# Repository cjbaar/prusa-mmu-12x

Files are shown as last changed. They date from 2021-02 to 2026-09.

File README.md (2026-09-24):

# ⚠️ **WARNING** ⚠️

Prusa is now blocking tool commands for community mods like this
on the CoreOne/L latest firmware. Unless they decide to reverse course,
upgrading past firmware version 6.5.7 will break this version of the
MMU3 with a hard-reset and error message mid-print. The firmware has
been locked-down to accept only T0-T4 commands. Working around this
now requires comiling custom firmware, and invalidating your printer's
warranty to apply it.

To say I am disappointed with this approach is an understatement. This
is not in the spirit of open source on which Prusa was founded.
I will not be purchasing any more printers from Prusa Research in the future.

# Prusa MMU2/MMU3 Modification for 12 Filaments
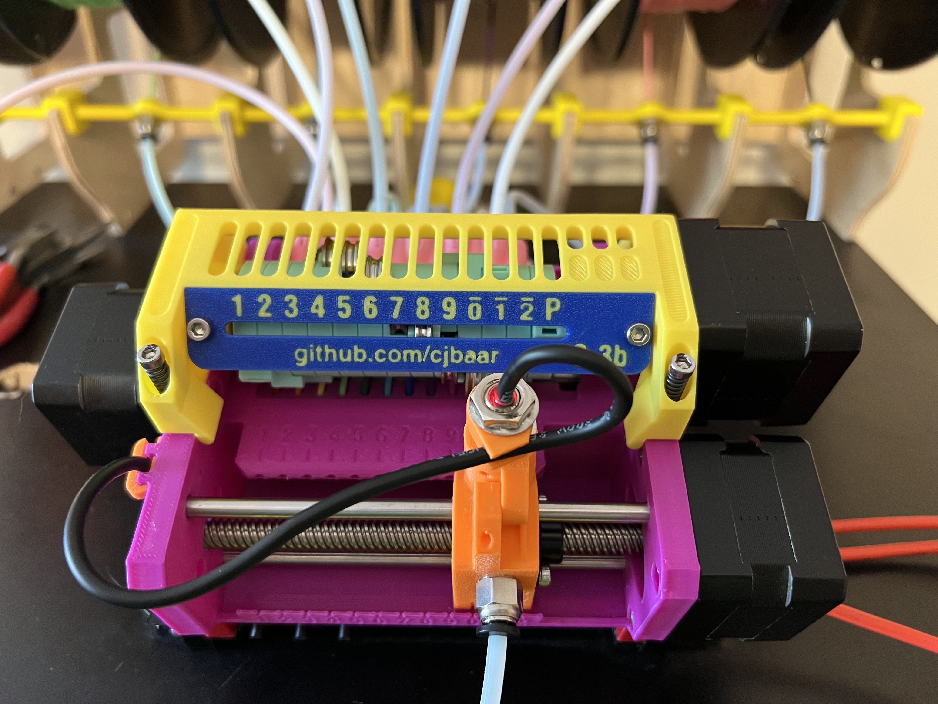
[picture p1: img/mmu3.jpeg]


## Overview

This is the result of several months of designing and testing new ideas for increasing the filament count of the Prusa MMU2S. (And then more testing and re-designs for the MMU3.)
I tried several variations, but ended up coming back to something that is largely based
on the original Prusa model. Some of the major adjustments include:
* increased filament count from 5 to 12
* reversed position of pulley and idler motors, to maximize the use of the 110mm pulley shaft
* moved FINDA to the rear of the selector, in an attempt to minimize issues where the filament clears the ball but then still fails to fully retract
* quick-release insert for FINDA sensor, for ability to clean or check ball chamber without re-calibration of FINDA height
* selector has integrated threads for PTFE quick-connect
* moved control board beneath the body (inspiration thanks to [univeraljoint](https://www.thingiverse.com/universaljoint/about))
* additional bracket mounting options
* selector does not include the cutter

As of October 2024, this project has been updated to include the MMU3 with the Mk4.
New features now also include:
* a new idler alignment gauge of the front side of the upper frame
* a streamlined idler design
* a smaller inlet that uses the PTFE collets instead of M10 screw connectors
* a cover panel for the power connection board

## The Disclaimer

*These items and related code are provided as-is, with no warranty -- express or implied -- and I cannot personally guarantee that it will function and/or not break your printer. Nothing here, of course, is officially endorsed or supported by Prusa.*

*(That being said, I -- and others -- have had a great deal of luck using this model, or I wouldn't be sharing it.)*

## Firmware

See update notes on version [3.0.4](https://github.com/cjbaar/prusa-mmu-12x/discussions/51).

### The Good News

Prusa has completely re-written the firmware for the MMU3. It is incredibly
clean and organized, and makes wonderful and proper use of configuration variables.
*(Thank you Prusa!)*
We no longer need to use custom firmware anymore, for either the MMU board
or the printer itself!

You can use the [`config.h`](./firmware/config-mmu3-mk4-12x.h) file provided here, and do your
own build with the [Prusa MMU Firmware](https://github.com/prusa3d/Prusa-Firmware-MMU) repo. I would generally encourage you to become familiar with the build process if you want to proceed
with this project. I will probably not be compiling this into every new version that Prusa
releases. However, you can download a compiled version of the current (as of now)
[3.0.3 firmware here](./firmware/cjb_fw_mmu3_3.0.3-x12.hex), or view
[my firmware fork here](https://github.com/cjbaar/Prusa-Firmware-MMU-12x).

NOTE: This version of the MMU3-12x will function exactly like the
stock Prusa MMU3, as it is entirely their firmware with a few different distance
numbers. It will use the new communication protocols, and report error messages
back to the printer screen. I personally found my interface "tweaks" easier to use and
understand, but this keeps things simpler. With the amount of work Prusa has to the
stock code, it just doesn't make sense to try re-writing it anymore.

### The Potential (Unknown) News

At the moment, flashing the MMU firmware is a relatively simple process, and the current
stock printer firmware does not block filaments above slot 5 -- even though it does not
understand how to process or access them from the menu functions.

As of now (Oct 2024), Prusa is currently working toward a firmware model wherein
the printer will retain a 
copy of the MMU firmware, and be responsible for updating it as necessary. I have no
idea how those changes will affect the ability to side-load custom firmware onto
the MMU directly. If we have to get into changing the printer firmware itself, things
become more complicated. We will have to wait and see for now.

__Update 03/2026__: I am still using stock printer firmware (6.5.3) without issue. There is no need to use custom printer firmware with the MMU3.

## Hardware

### Printed Parts
Print one of each included STL file, with the following exceptions:
* choose either m6 or m10 thread for selector base
	* or original m5 heat-set remix, thanks to [obe](./remixes/obe)
* choose bracket type (traditional frame mount or table-top)
* print four copies of idler-rings.stl

I printed all parts with on a Prusa Mk4 using the "Structural" input-shaping profile.
All are printed with 0.2mm layers and 20% infill.

I also print everything with PLA, because I get better consistency and tolerances for bearings and general fit. In my experience, printing the same model in PETG (or other material) may make some pieces harder to fit together.

For the "lower" model, there is a related mod file, which I recommended printing with 100% infill. The selector cap might also need to be 100% infill.

### Additional Parts

The following pieces are required for assembly. Items in italics may not be included in the original Prusa MMU3, but should be easily found on Amazon (or your world-domination retailer of choice).

#### Lower
* (1x) Prusa MMU "Pulley" motor (110mm d-shaft)
* (1x) Prusa MMU "Selector" motor (120mmx8mm lead screw)
* (12x) m3x10mm screw
* (6x) m3 square nut
* (4x) 625Z bearing
* (2x) 5mmx120mm steel rod
* *(7x) 12mmx12mmx5mm drive gear (40T)*\
	NOTE: I have a hard time finding actual 12mm wide gears now. All the ones I have purchased lately on Amazon claim to be 12mm, but are actually only 11mm. These may cause issues with filament allignment.

#### Upper
* (1x) Prusa MMU "Idler" motor (std d-shaft)
* (3x) m3x10mm screw
* *(2x) m5x16mm screw*
* (2x) m3x30mm screw
* (2X) m3x6mm screw
* (2x) m3x15mm spring
* (2x) m3 square nut

#### Idler
* *(12x) m3x20mm screw*
* (12x) m3 hex nut
* *(1x) 608RS bearing*
* *(12x) 4x13x4mm u-shaped bearing*
* *(1x) 5mmx100mm steel rod*

#### Microcontoller Unit (MCU)
* *(4x) m3x14mm screw*
* *(3X) m3x12mm screw*
* (1X) m3x6mm screw
* (3x) m3 hex nut
* (1x) m3 square nut

#### Inlet
* *(2x-6x) m2x16mm screw*
* *(2x-6x) m2 hex nut*
* (12x) PTFE collet

#### Selector
* *(2x) m3x8mm screw*
* *(2x) m3x16mm screw*
* (2x) m3 square nut
* (2x) m3 hex nut
* (1x) T8 plastic lead screw nut
* *(1x) m10 OR m6 PTFE quick-fit connector*
* (2x) 5mm brass sleeve, cut to 20mm length
* (1x) FINDA sensor
* (1x) Sensor ball

#### Brackets
* *(2x) m3x8mm screw*

## Images
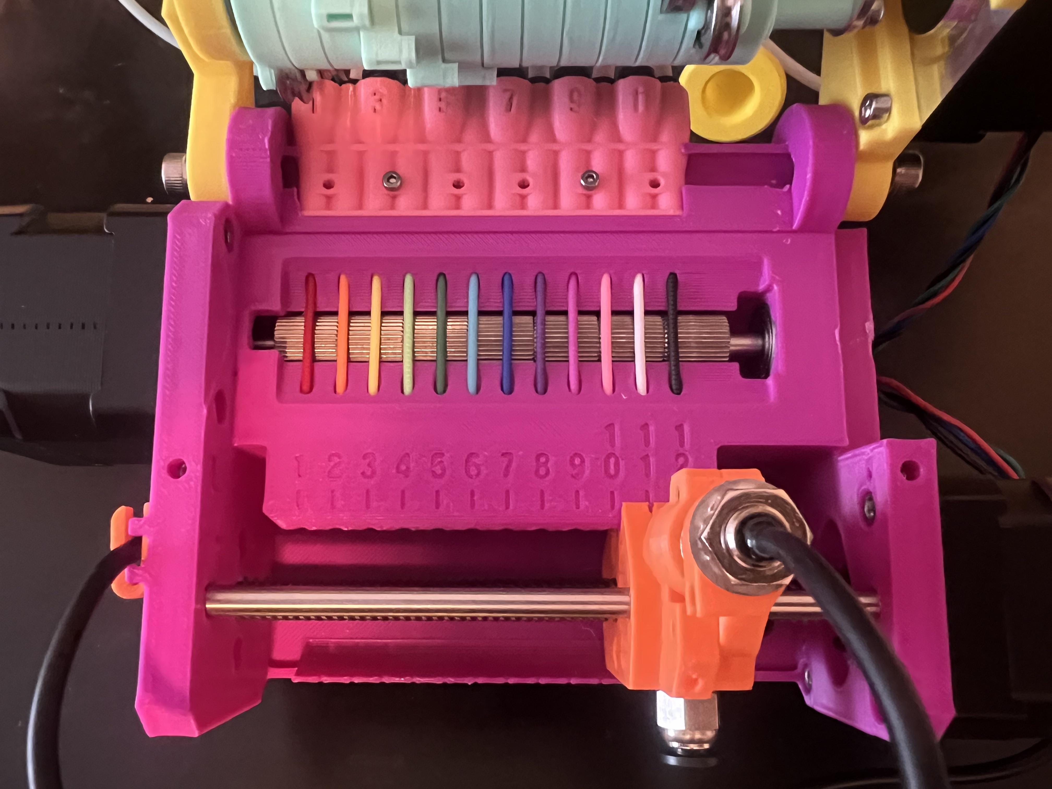
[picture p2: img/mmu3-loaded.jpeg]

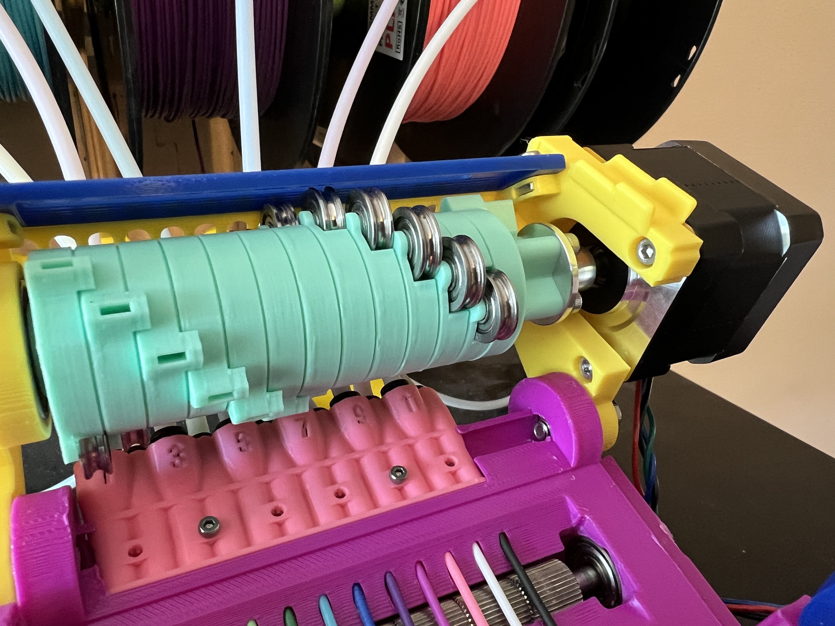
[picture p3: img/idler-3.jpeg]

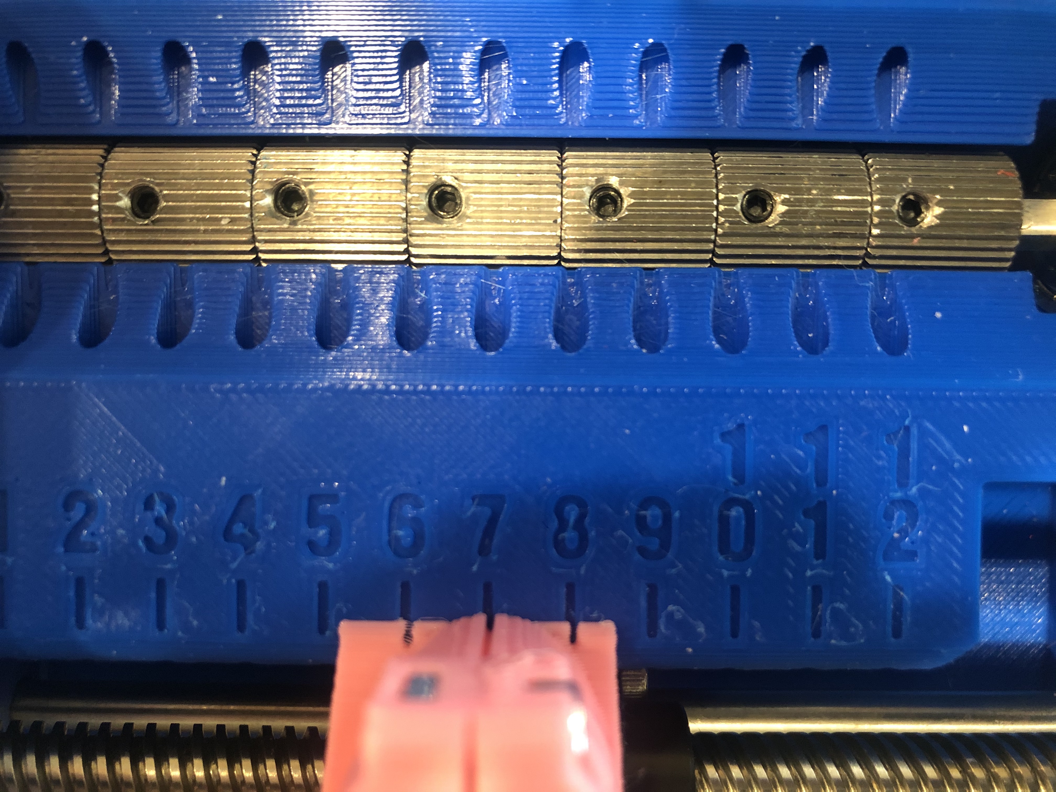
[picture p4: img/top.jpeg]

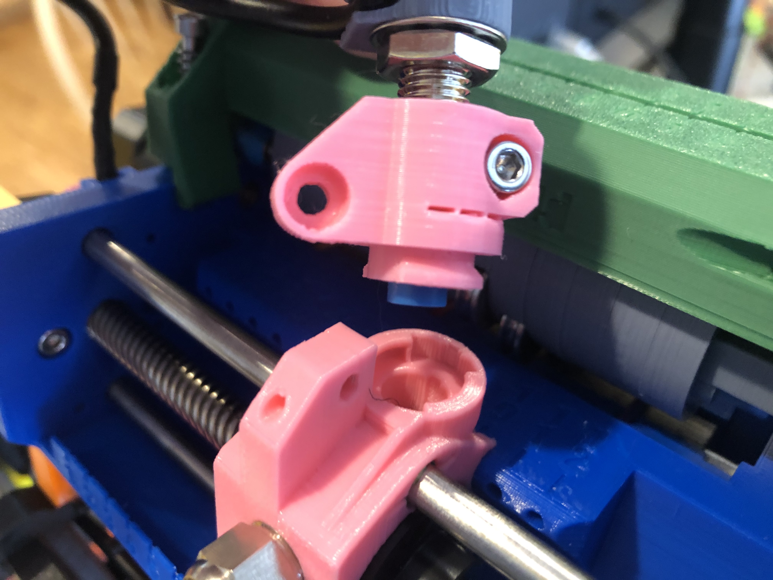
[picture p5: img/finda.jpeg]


## Testing
Full setup with spool rewinders from [VincentGroenhuis](https://www.thingiverse.com/thing:3781815/files)

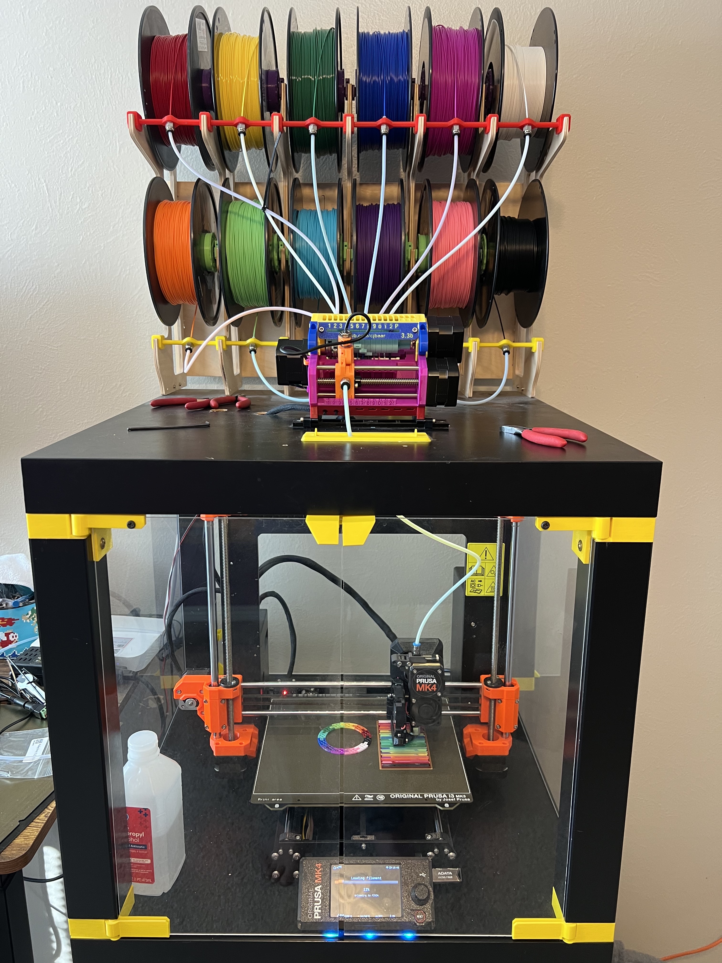
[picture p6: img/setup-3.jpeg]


## Output
A successful 12-color print.

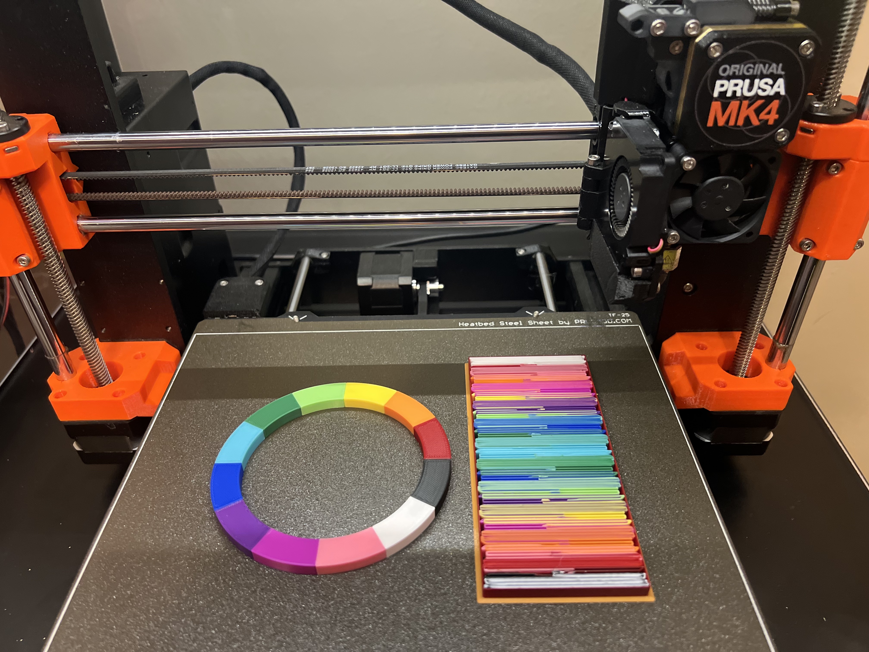
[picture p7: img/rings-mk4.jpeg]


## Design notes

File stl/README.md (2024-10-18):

# Prusa MMU Modification for 12 Filaments

## Directory

#### v1.4
Files for the older (MMU2/MMU2S+Mk3) version.

#### v3.3
Current files for the MMU3+Mk4.

*To avoid confusion (or perhaps incur more of it), I skipped to version 3,
to align with the MMU version number.*

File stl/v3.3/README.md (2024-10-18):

# Assembly Tips

As this project has started to gain popularity, several people have asked for more detailed
build instructions. Being a pet project, I don't have any official documentation. In general,
the files provided assume that you have previously built the stock Prusa MMU3, and are probably
re-using many of the parts. Below are some of the major differences from the stock model.

## Pulley

The pulley motor is moved to the left, to make full use of its length. Install a 625Z bearing
on each side of the pulley chamber, and start feeding the motor shaft in from the left of the
unit. As you go, install the seven 40T gears. As shown here, try to align the gears so that no
filament will end up on a grub screw. The even-numbered filaments will end up in the very narrow
space between the edge of a gear and its grub screw.

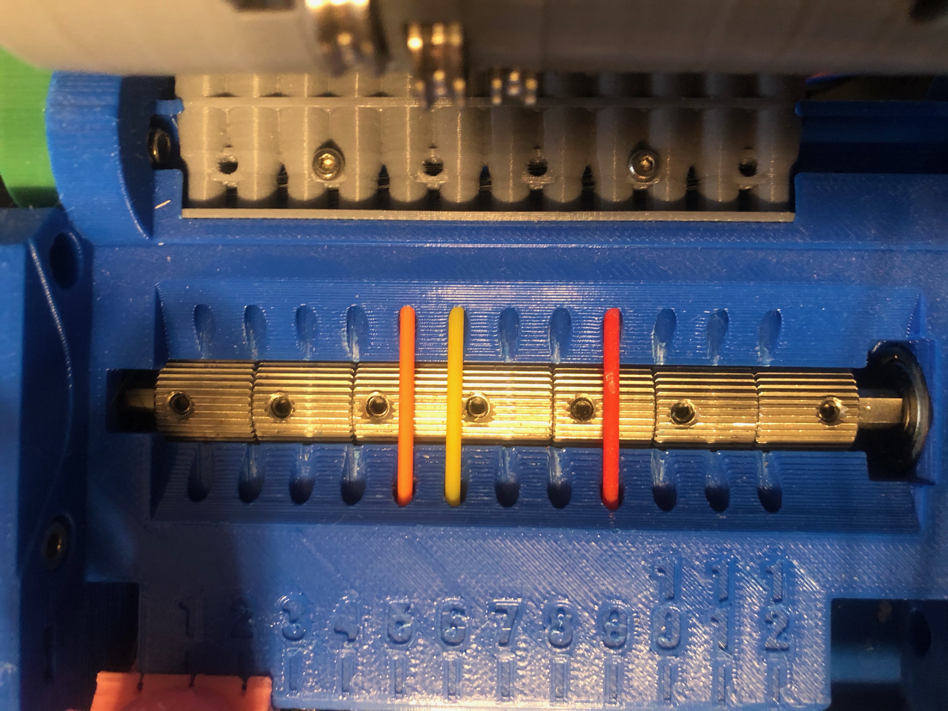
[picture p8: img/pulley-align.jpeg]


## Inlet

The inlet now uses the PTFE collets including with the MMU3 kit. It needs 12, so I used
the ones from the buffer/roller kits as well (I don't use them). If you don't have enough,
or you prefer the M10 screw PTFE locks, you can print the old inlet from the v1.4 folder.
Both models fit in the lower frame the same, and can be held with a couple of M2 screws.

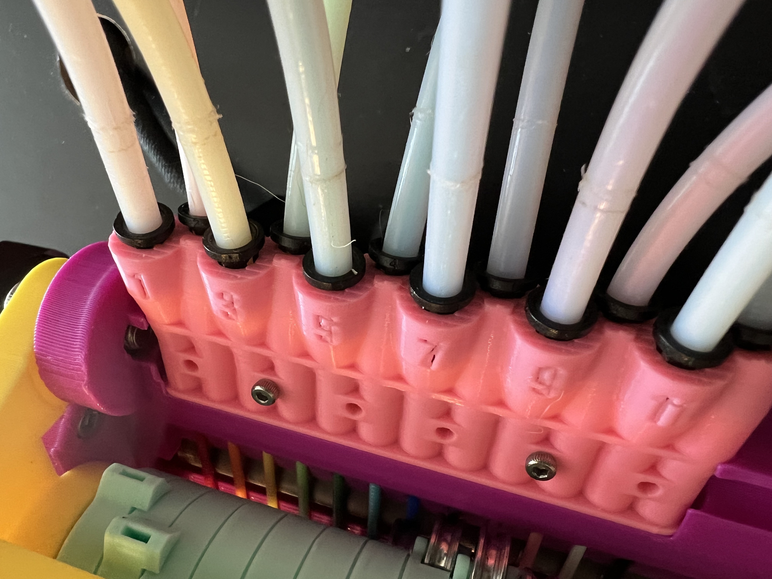
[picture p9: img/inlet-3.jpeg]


## Idler

This is the most major change, as the idler has to be assembled from many pieces. Start with
the a ring labeled "3" for the bottom, and add the rings in groups of three. Each ring
has a printed number (1,2,3) on the bottom, so install in order, and make sure the screw holes
line up. Place hex nuts in the end piece, and in each "#3" piece, and then after each set
install the M3 screw. These screws are probably optional, but I use them to help keep the
alignment snug. Do not tighten the screws past the point where they are seated, or it could
compress the overall size of the idler.

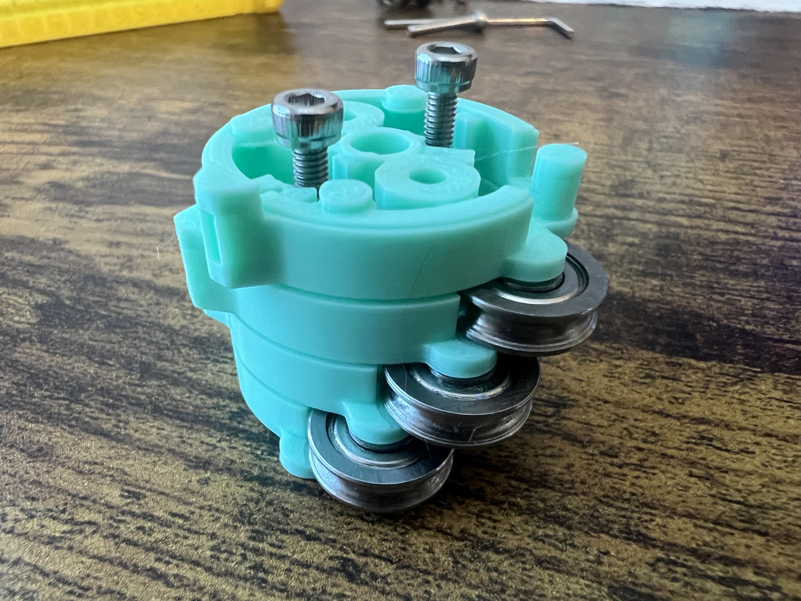
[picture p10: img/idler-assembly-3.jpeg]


Before installing the top end, make sure to inset 4x M3 hex nuts. These will hold the metal
motor mount (included with the Prusa MMU3 kit).

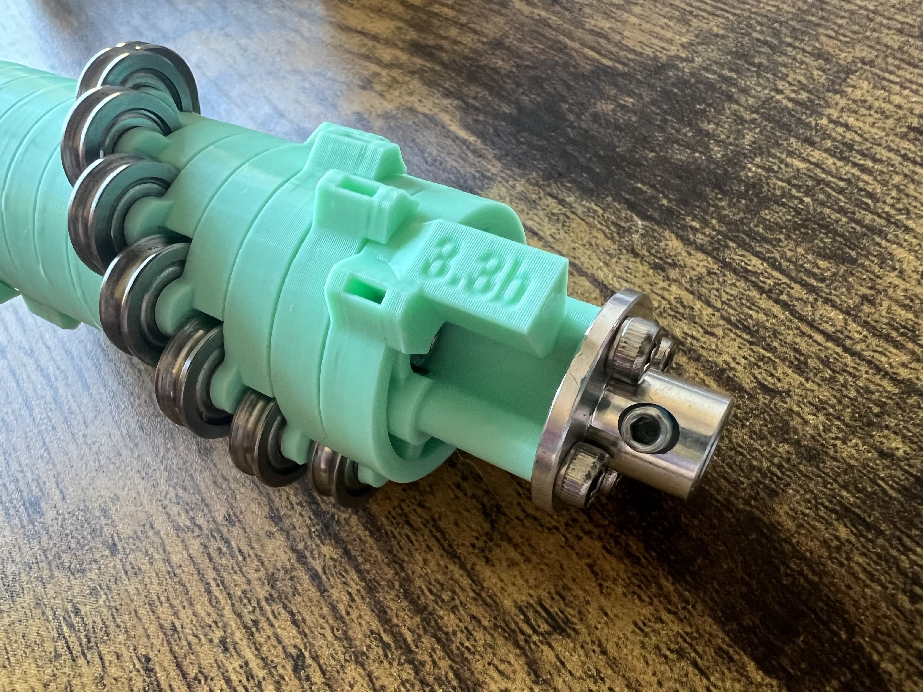
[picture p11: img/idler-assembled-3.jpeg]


Finish the lower end of the assembly with the small cap from idler-ends.stl.
The cap fits into a 608RS bearing, which in turn fits into the upper frame.
Install the assembly into the upper piece, using m3 screws to mount the motor.
Tighten the grub screws, while keeping the assembly pushed as far to the left as it
will go (up against the bearing).
This should provide proper alignment with the filament slots.



Print either the single or two-color model for the faceplate (upper-panel.stl/upper-color.stl).
Install the panel with two square nuts and 6mm screws.
Once completed, the slot on each ring should align through the small window when that
filament is engaged, or when the idler is parked at the end.



## Power Board

Prusa has solved the previous MMU power issues by providing a new power board. On the
stock model, this hangs off the back of the idler. Since this model mounts the MCU
under the main body, my solution is just to bend the right-angle headers back to
straight. There is a printed cover to add-on once the board is installed.

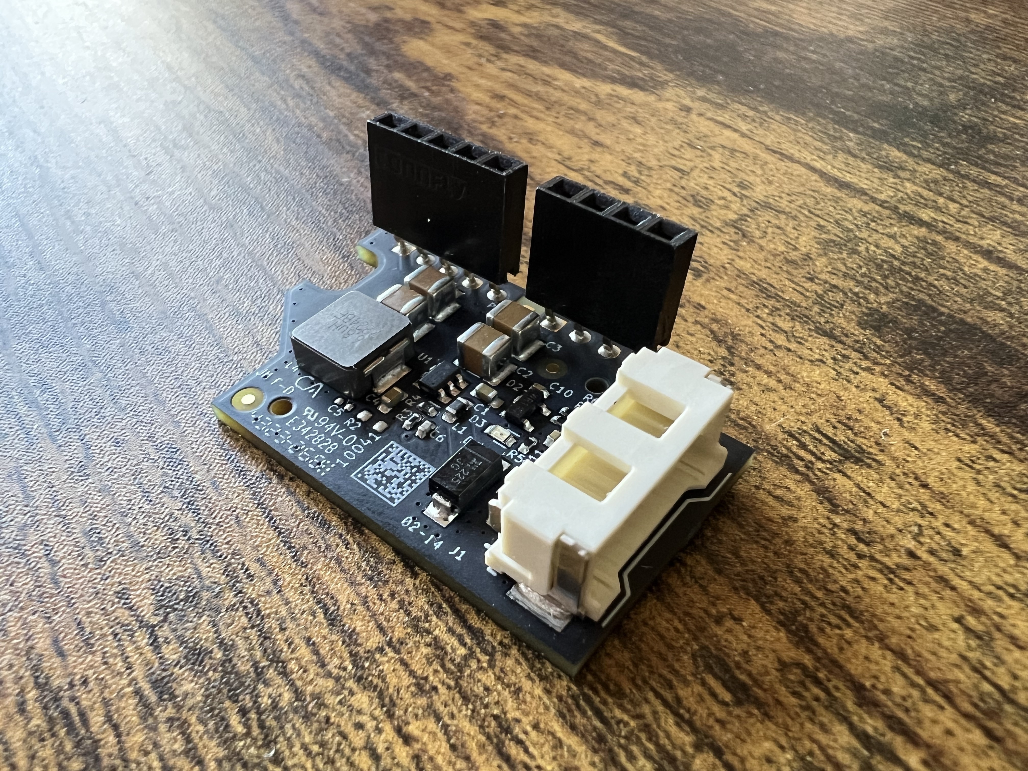
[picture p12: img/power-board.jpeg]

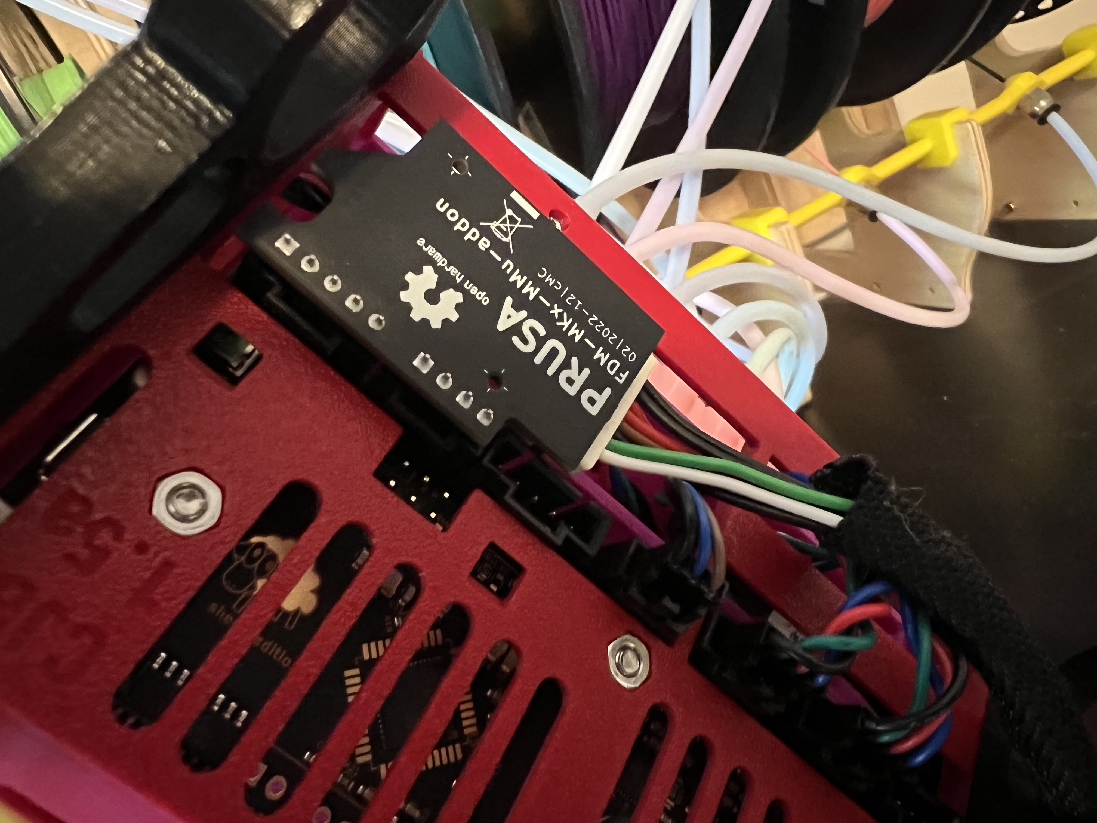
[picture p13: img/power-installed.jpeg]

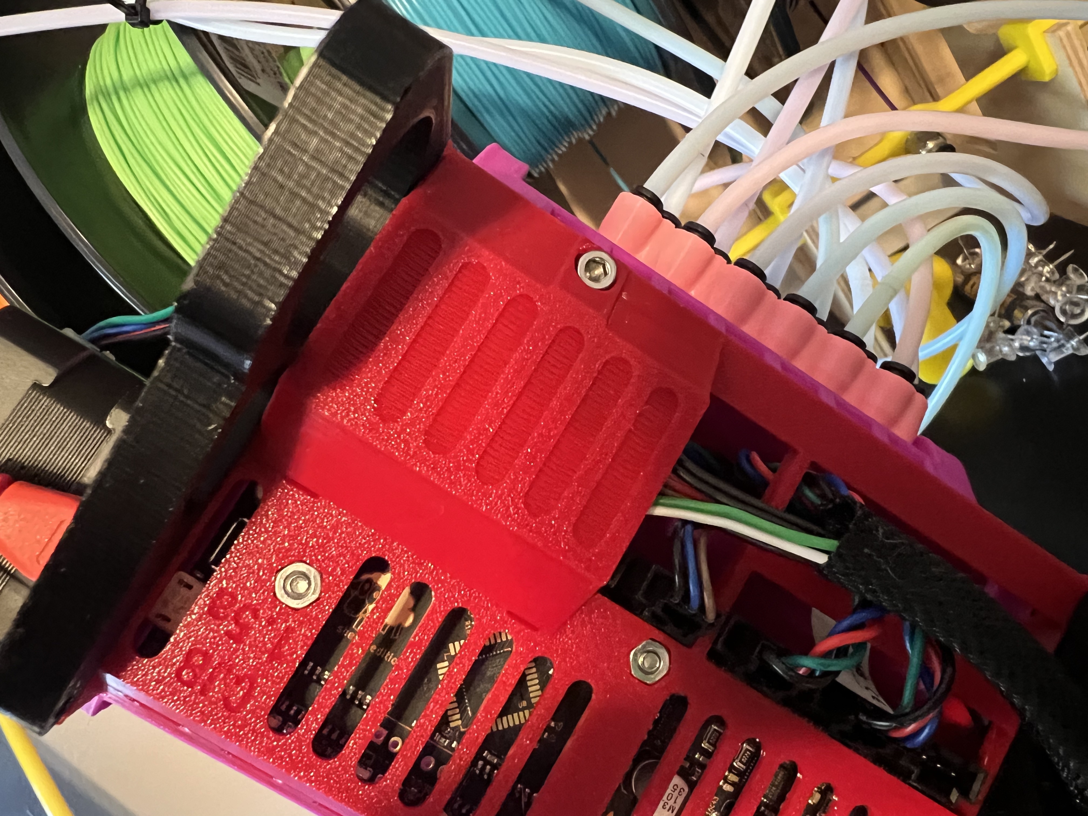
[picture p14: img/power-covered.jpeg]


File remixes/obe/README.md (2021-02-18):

Special thanks to Thingiverse user [obe](https://www.thingiverse.com/obe/designs) for sharing 
a remix of the selector that works with the original Prusa m5 heat-set insert.

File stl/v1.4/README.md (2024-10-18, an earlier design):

# Prusa MMU2S Modification for 12 Filaments
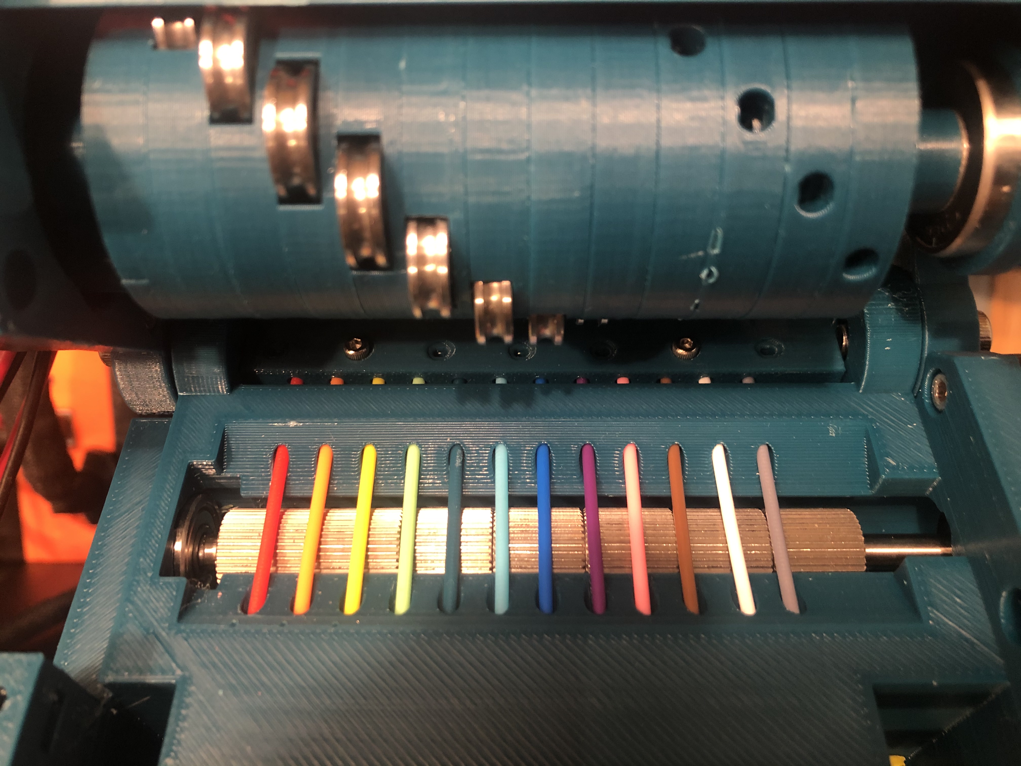
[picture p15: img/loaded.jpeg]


## Overview
This is the result of several months of designing and testing new ideas for increasing the filament count of the Prusa MMU2S. I tried several variations, but ended up coming back to something that is largely based on the original Prusa model. Some of the major adjustments include:
* increased filament count from 5 to 12
* reversed position of pulley and idler motors, to maximize the use of the 110mm pulley shaft
* moved FINDA to the rear of the selector, in an attempt to minimize issues where the filament clears the ball but then still fails to fully retract
* added quick-release for FINDA sensor, for ability to clean or check ball chamber without re-calibration of FINDA height
* selector has integrated threads for PTFE quick-connect
* moved control board beneath the body (inspiration thanks to [univeraljoint](https://www.thingiverse.com/universaljoint/about))
* additional bracket mounting options
* optional integrated OLED display for more detailed state information and enhanced error recovery
* selector does not include the cutter

## The Disclaimer
These items and related code are provided as-is, with no warranty -- express or implied -- and I cannot personally guarantee that it will function and/or not break your printer. Nothing here, of course, is officially endorsed or supported by Prusa.

That being said, I have had a great deal of luck using this model, or I wouldn't be sharing it.

## Software & Firmware
In order to use this model of the MMU, you will need to use the following modified firmware for the MMU board. This has been branched from version 1.0.6, but has numerous significant changes, so whether or not I will keep this up-to-date with future version is questionable.

https://github.com/cjbaar/MM-control-01

In addition, you will need to change the firmware on the printer itself, because the existing code will ignore any tool changes above T4. This is now based on branch 3.11.0. There is a compiled version for the MK3S in the firmware folder of this repo.

https://github.com/cjbaar/Prusa-Firmware/tree/MK3_3.11.0

Finally, in order to create the gcode files, you will need to create a new printer model in a MMU-aware slicer that is setup for 12 filaments. I had no issues doing this in PrusaSlicer version 2.1.0+.

## Hardware
### Printed Parts
Print one of each included STL file, with the following exceptions:
* choose either m6 or m10 thread for selector base
	* or original m5 heat-set remix, thanks to [obe](./remixes/obe)
* choose bracket type (traditional frame mount or table-top)
* print four copies of idler-rings.stl
* screen is optional, if using OLED display
* wrench is optional, but assists with assembling the inlet manifold

I printed all parts with relatively slow speed and 0.2mm layers. I also printed most everything with PLA -- in particular, the selector and idler rings -- because I get better consistency and tolerances for bearings and general fit. In my experience, printing the same model in PETG may make some pieces harder to fit together.

For the "lower" model, there is a related mod file, which I recommended printing with 100% infill. The selector cap might also need to be 100% infill.

### Additional Parts
The following pieces are required for assembly. Items in italics may not be included in the original Prusa MMU2, but should be easily found on Amazon (or your world domination retailer of choice).

#### Lower
* (1x) Prusa MMU "Extruder" motor (std d-shaft)
* (1x) Prusa MMU "Pulley" motor (110mm d-shaft)
* (1x) Prusa MMU "Selector" motor (120mmx8mm lead screw)
* (12x) m3x10mm screw
* (6x) m3 square nut
* (4x) 625Z bearing
* (2x) 5mmx120mm steel rod
* *(7x) 12mmx12mmx5mm drive gear (40T)*

#### Upper
* (4x) m3x10mm screw
* *(2x) m3x12mm screw*
* *(2x) m5x16mm screw*
* (2x) m3x30mm screw
* (2x) m5x15mm spring

#### Idler
* *(6x) m3x20mm screw*
* *(2x) m3x25mm screw*
* (10x) m3 hex nut
* *(1x) 608RS bearing*
* *(12x) 4x13x4mm u-shaped bearing*
* *(1x) 5mmx100mm steel rod*
* *(2x) 11mmx11mmx5mm Mk8 brass drive gear (26T)*

#### Microcontoller Unit (MCU)
* *(4x) m3x14mm screw*
* *(3X) m3x12mm screw*
* (3x) m3 hex nut

#### Inlet
* *(6x) m2x16mm screw*
* *(6x) m2 hex nut*
* *(12x) m10 PTFE quick-fit connector*

#### Selector
* *(2x) m3x8mm screw*
* *(2x) m3x16mm screw*
* (2x) m3 square nut
* (2x) m3 hex nut
* (1x) T8 plastic lead screw nut
* *(1x) m10 OR m6 PTFE quick-fit connector*
* (2x) 5mm brass sleeve, cut to 20mm length
* (1x) FINDA sensor

#### Brackets
* *(2x) m3x8mm screw*

#### Display (optional)
* *(1x) OLED SSD1306 display, I2C, 128x64*
* *(4x) m2x8mm screw*
* *(1x) m3x8mm screw*
* (1x) m3 square nut
* *(4x) 200mm F/F jumper wires*

## Images
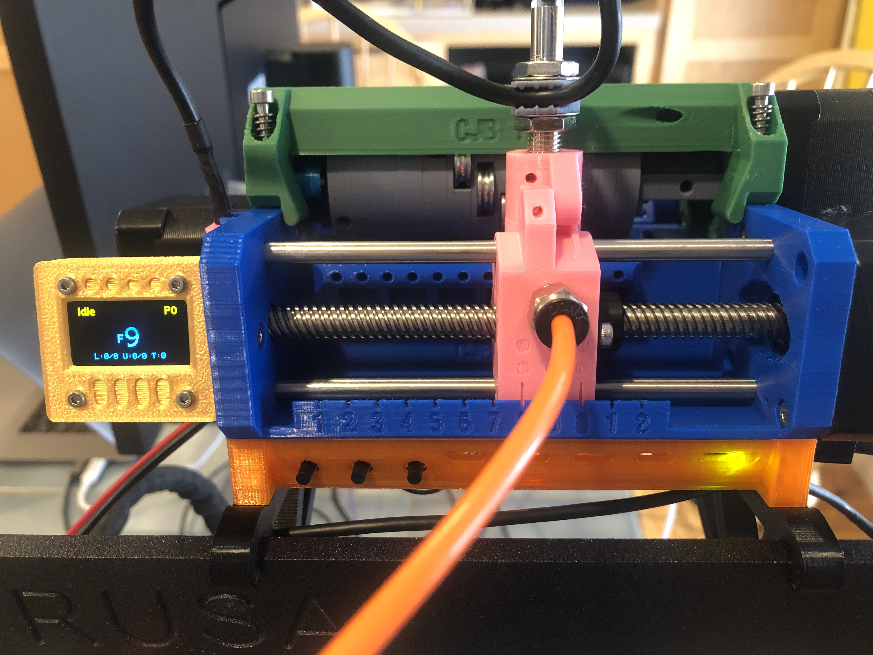
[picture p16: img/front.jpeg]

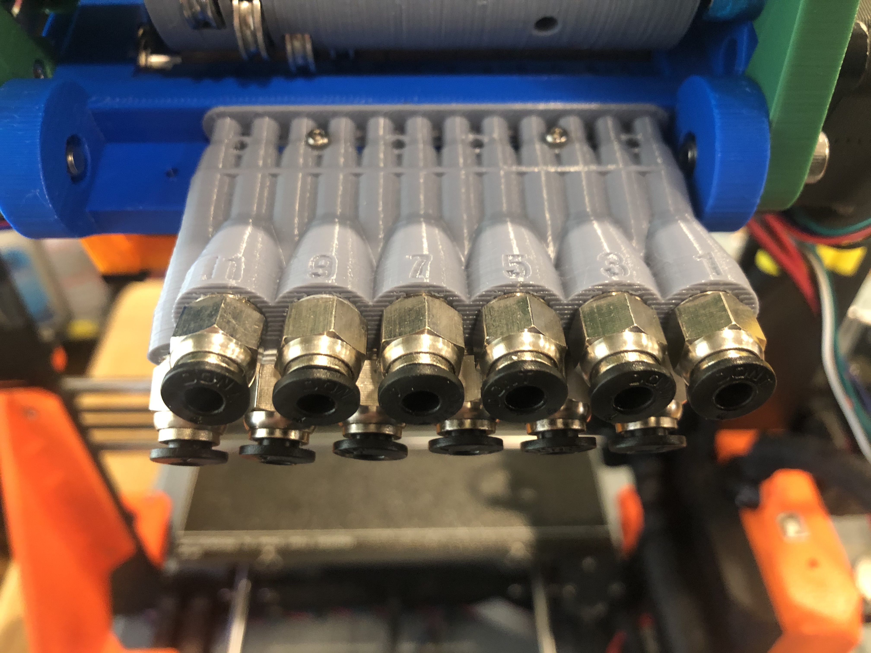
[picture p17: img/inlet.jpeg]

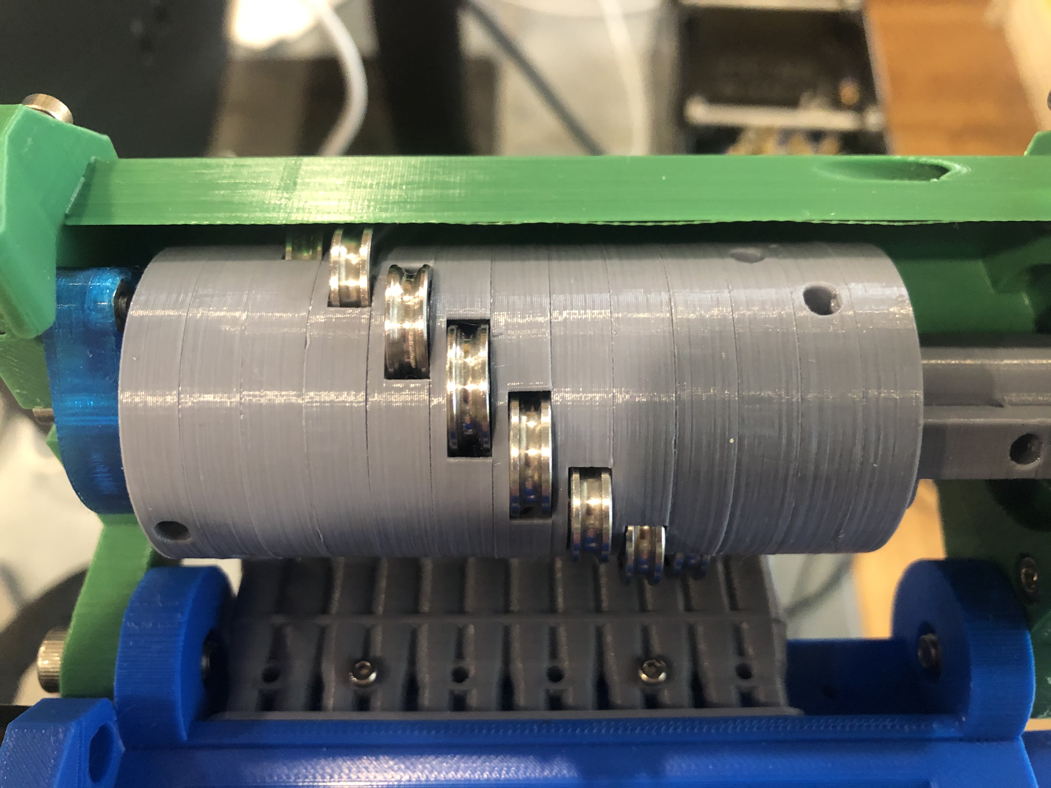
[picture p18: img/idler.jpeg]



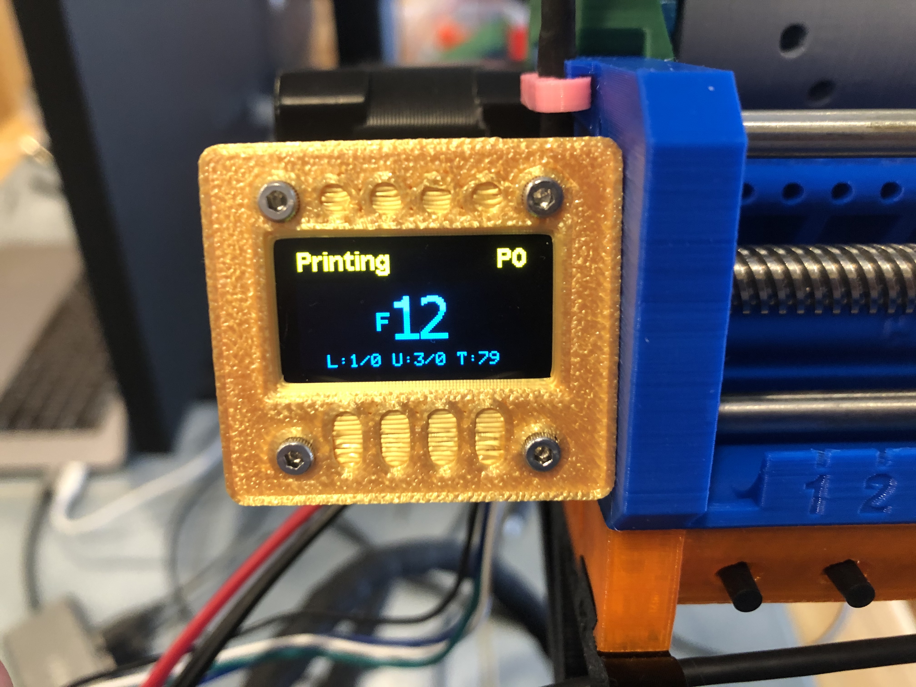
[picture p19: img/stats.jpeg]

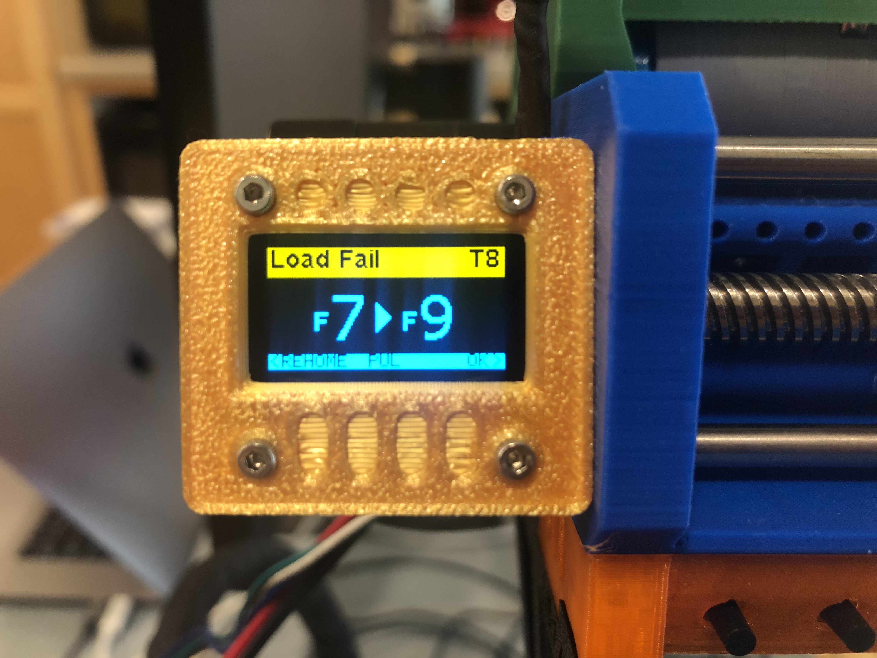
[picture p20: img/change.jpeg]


## Testing
Full setup with spool rewinders from [VincentGroenhuis](https://www.thingiverse.com/thing:3781815/files)

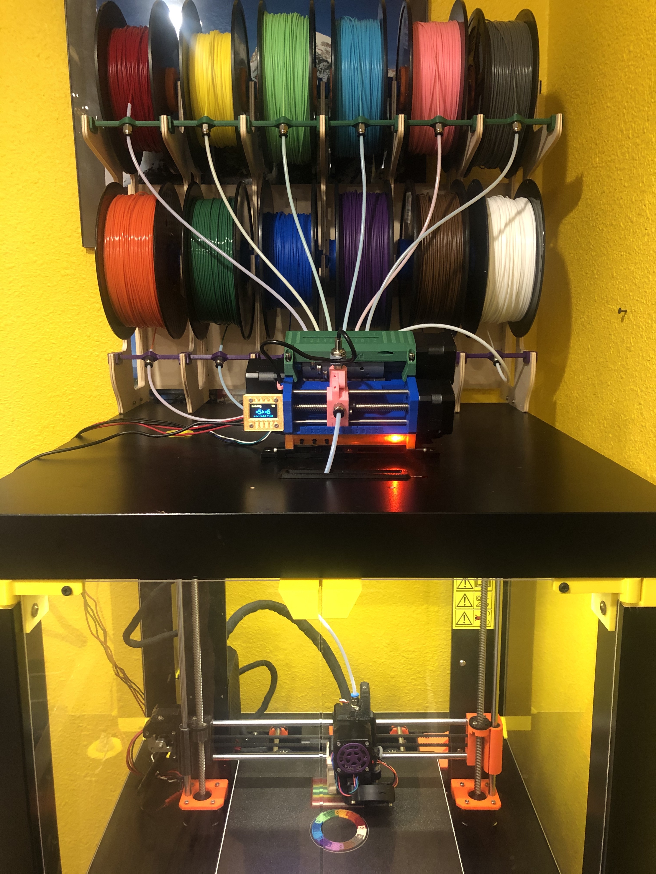
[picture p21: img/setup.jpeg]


## Output
A successful 12-color print

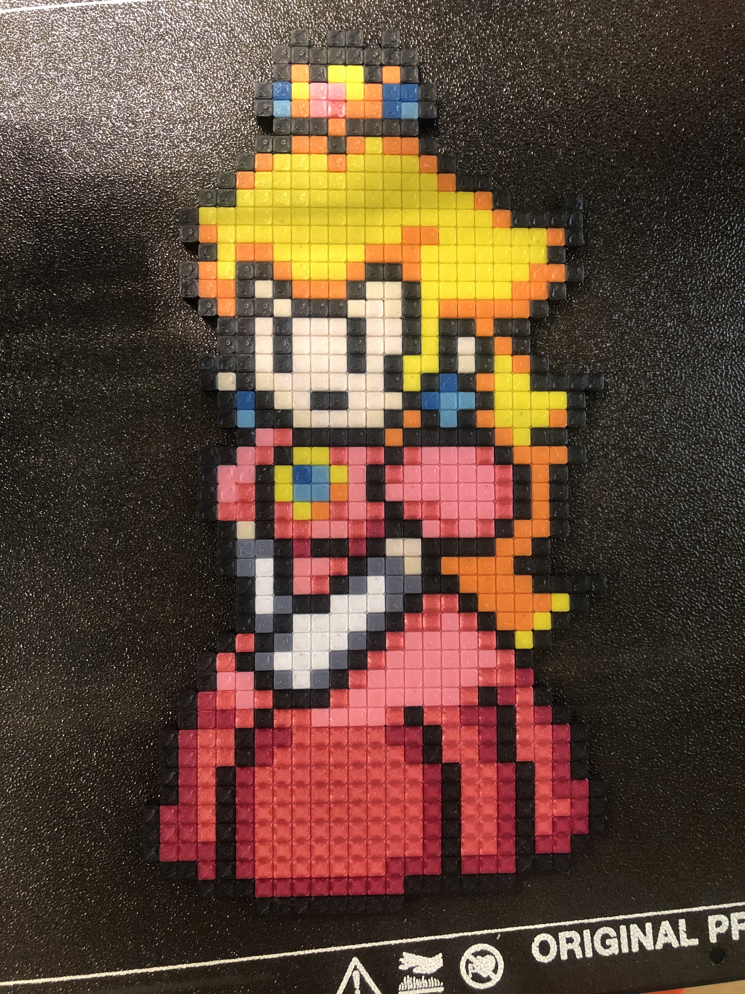
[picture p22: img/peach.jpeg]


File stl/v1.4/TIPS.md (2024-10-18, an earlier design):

# Assembly Tips

As this project has started to gain popularity, several people have asked for more detailed
build instructions. Being a pet project, I don't have any official documentation. In general,
the files provided assume that you have previously built the stock Prusa MMU, and are probably
re-using many of the parts. Below are some of the major differences from the stock model.

## Pulley

The pulley motor is moved to the left, to make full use of its length. Install a 625Z bearing
on each side of the pulley chamber, and start feeding the motor shaft in from the left of the
unit. As you go, install the seven 40T gears. As shown here, try to align the gears so that no
filament will end up on a grub screw. The even-numbered filaments will end up in the very narrow
space between the edge of a gear and its grub screw.



## Idler

This is the most major change, as the idler has to be assembled from many pieces. Start with
the "top" (tall piece from idler-ends.stl), and add the rings in groups of three. Each ring
has a printed number (1,2,3) on the bottom, so install in order, and make sure the screw holes
line up. Place hex nuts in the end piece, and in each "#3" piece, and then after each set
install the M3 screw. These screws are probably optional, but I use them to help keep the
alignment tight.



Install the two 24T gears into the top; these secure the idler assembly to the motor spindle.
Align the grub screws with the holes, and open them to allow room for the motor spindle.
Slide the "top" end onto the motor spindle, aligning the flat side of the spindle with one pair
of grub screws. Tighten the screws on the flat side slightly to keep alignment, but do not 
tighten fully yet.

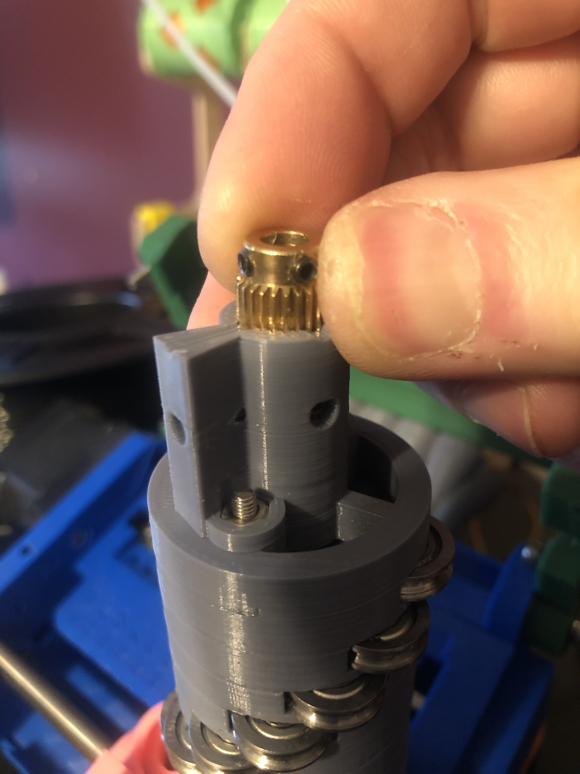
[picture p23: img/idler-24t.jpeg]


Finish the assembly with the small cap from idler-ends.stl. The cap fits into a 608RS bearing,
which in turn fits into idler-mount.stl.

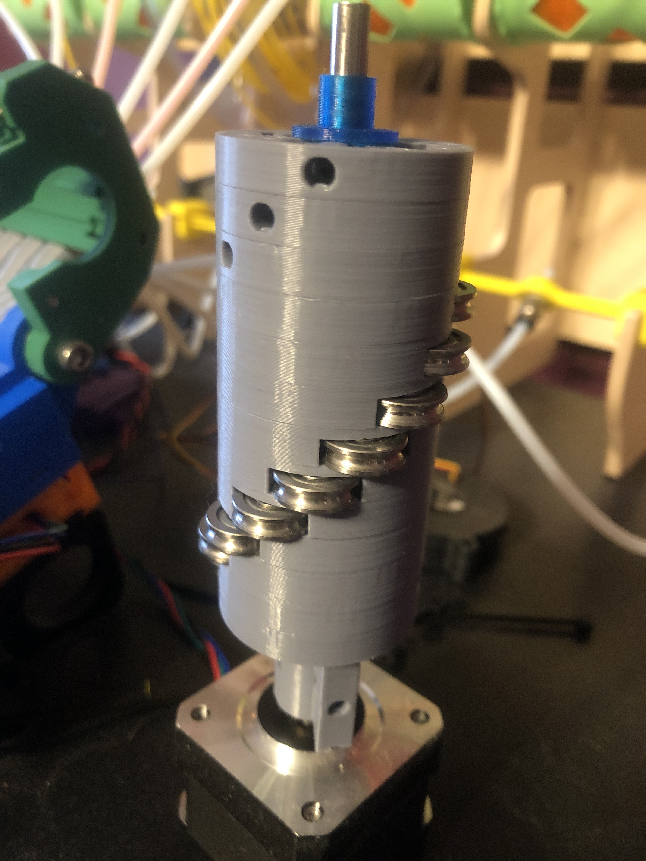
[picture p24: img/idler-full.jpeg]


At this point, install the assembly into the upper piece, using m3 screws to mount the motor
and the idler-end (hex nuts are required in the idler-end). Once the ends are secured, tighten
the grub screws, while keeping the assembly pushed as far to the left as it will go (up against
the bearing). This should provide proper alignment with the filament slots.



One last note on the idler design. The holes on each ring, opposite where the bearing fits,
was originally there to add a m2 screw on each ring. I stopped doing this when I added the 
internal m3 screws, but I did a long slot opening on the upper body. When a given filament
is "engaged," the hole on the ring should line up perfectly centered in the slot next to its
corresponding number. This helps to know if the idler has become out of expected alignment
during a print. This (terrible) photo shows filament #1 "engaged."

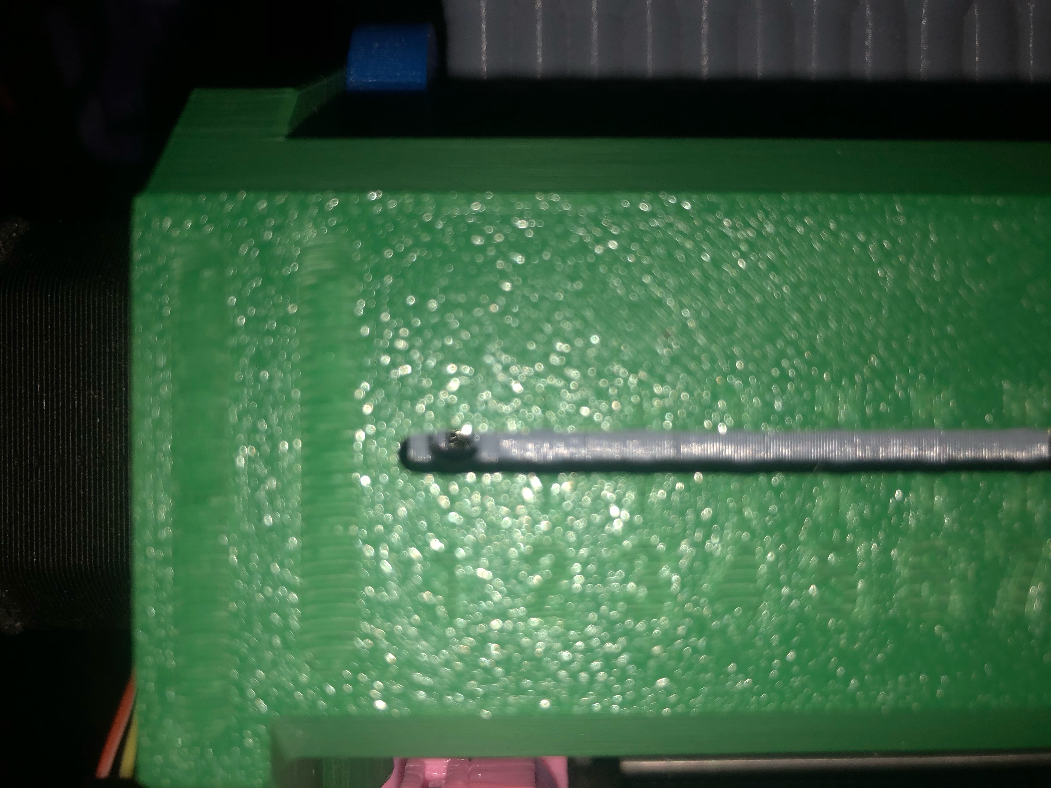
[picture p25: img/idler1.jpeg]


## Display

For the optional SSD1306 display, make sure you have a model that is set to use I2C communication.
Attach four wires from the display to the unused port on the control board, which
should be labeled as "SENSOR." (In reality, this port is just an unused-but-conveniently-exposed
I2C interface.)

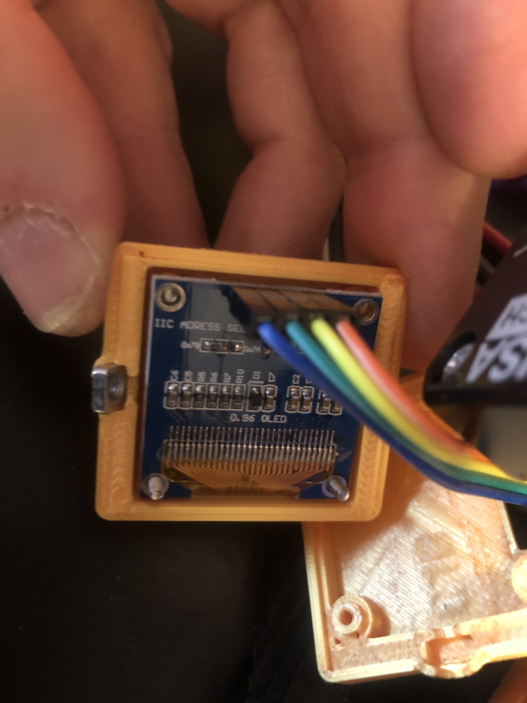
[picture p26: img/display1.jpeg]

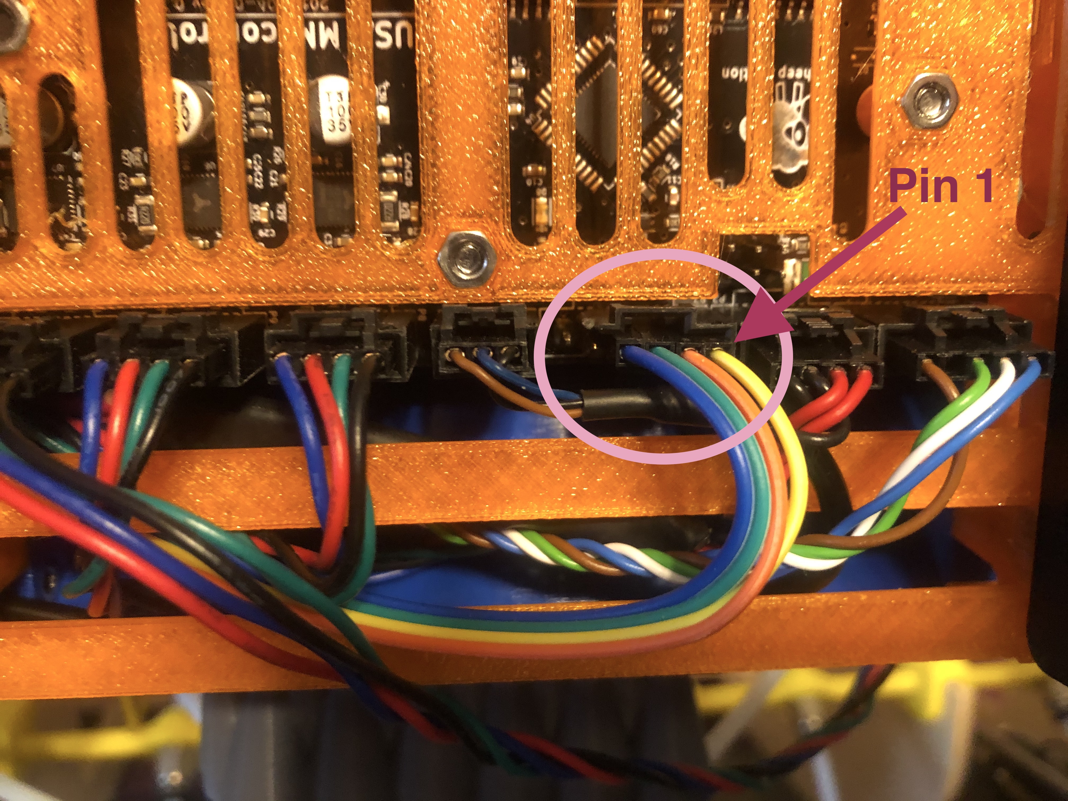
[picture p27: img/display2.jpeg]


Note the order of the colors, here; they are not the same on both sides. 
In case you have a different display, the actual pin connections should be as shown below.
Pin "1" on the control board is the one closest to the power connection. The colors listed
below are only in reference to the wires I used in the two photos above.
```
  1 <-> VCC (yellow)
  2 <-> GND (orange)
  3 <-> SCL (green)
  4 <-> SDA (blue)
```

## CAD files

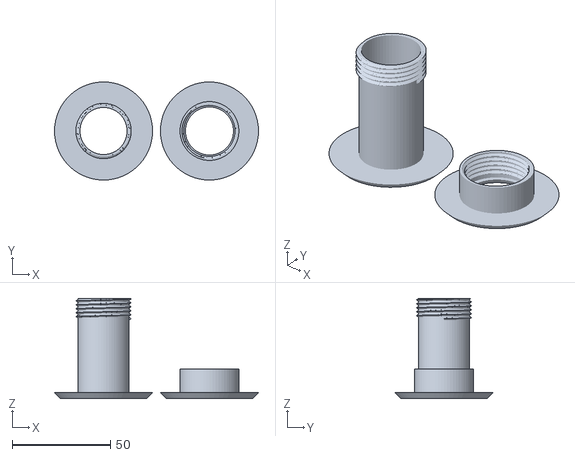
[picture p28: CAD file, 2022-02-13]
lack-enclosure-mods/cable-passthrough.stl
104.0 x 50.0 x 51.0

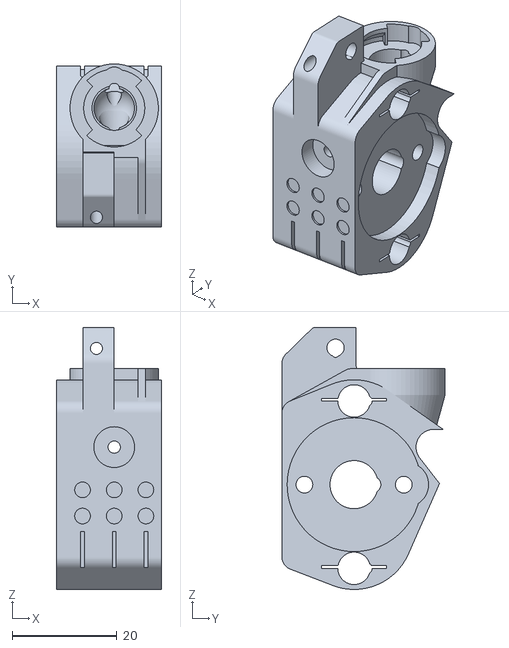
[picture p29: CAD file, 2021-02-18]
remixes/obe/HeatSet-mmu12x-selector-v1.1.stl
20.0 x 31.2 x 50.1

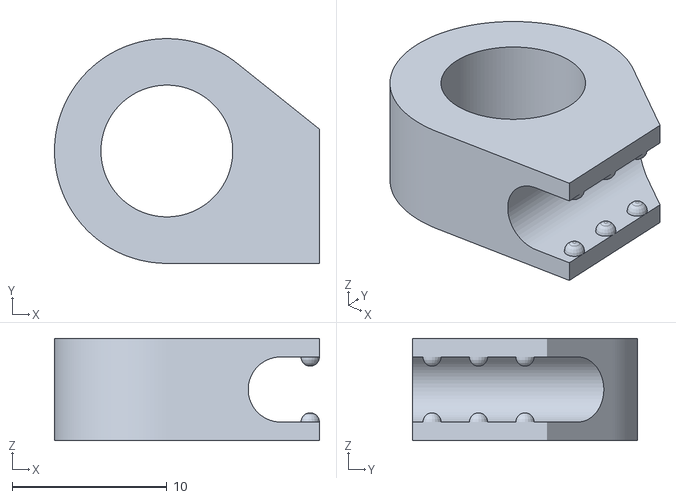
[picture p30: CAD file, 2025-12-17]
stl/v3.3/mmu12x-finda-clamp.stl
17.1 x 14.5 x 6.60

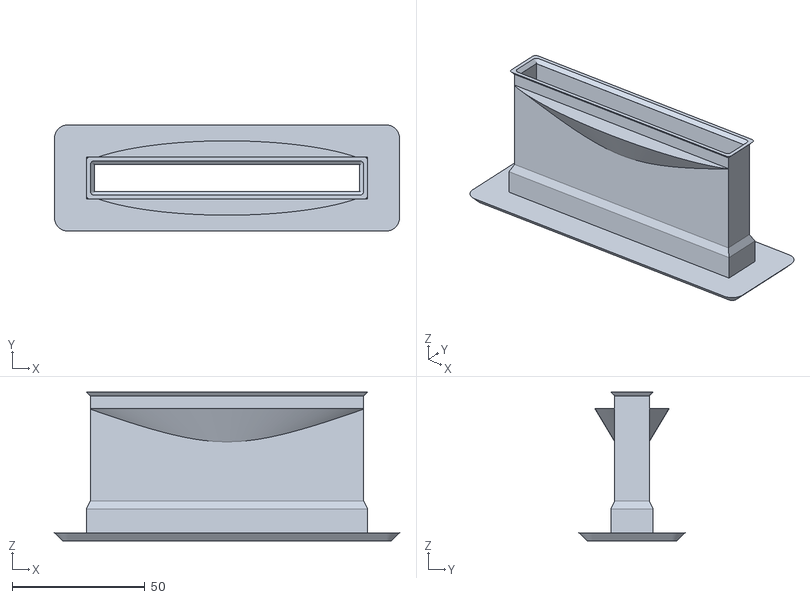
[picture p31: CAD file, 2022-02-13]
lack-enclosure-mods/mmu-ptfe-pass.stl
130.0 x 40.0 x 56.0

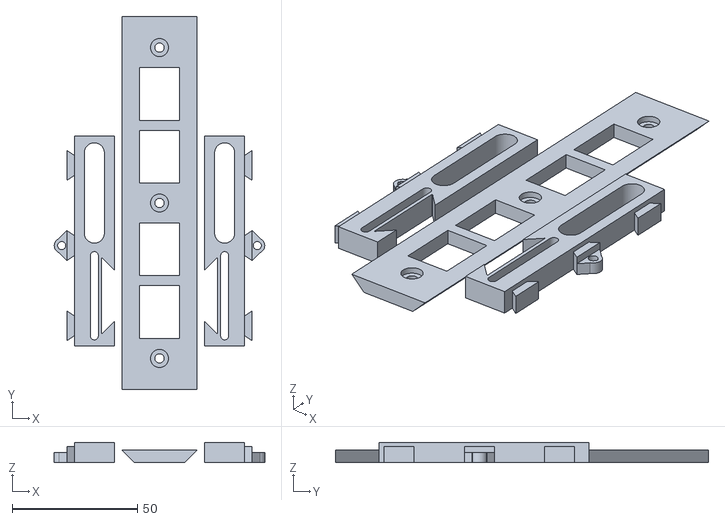
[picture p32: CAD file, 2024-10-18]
stl/v3.3/mmu12x-bracket-table.stl
84.0 x 148.8 x 8.00

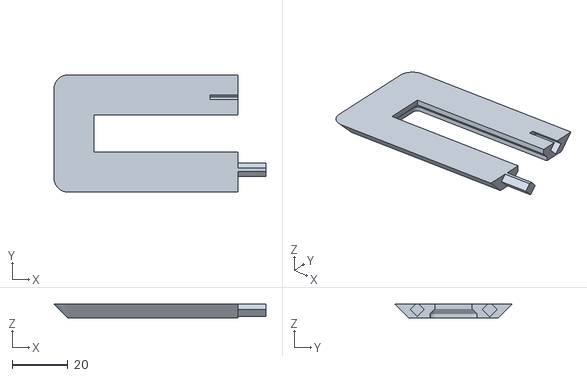
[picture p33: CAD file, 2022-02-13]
lack-enclosure-mods/mmu-ptfe-pass-lock.stl
76.0 x 42.0 x 5.00

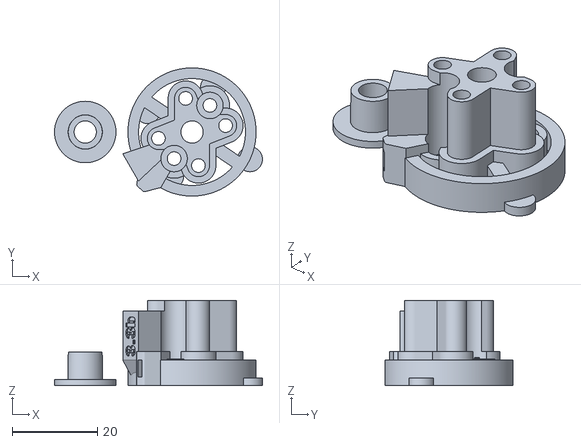
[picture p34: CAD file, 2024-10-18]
stl/v3.3/mmu12x-idler-ends.stl
48.7 x 30.0 x 20.0

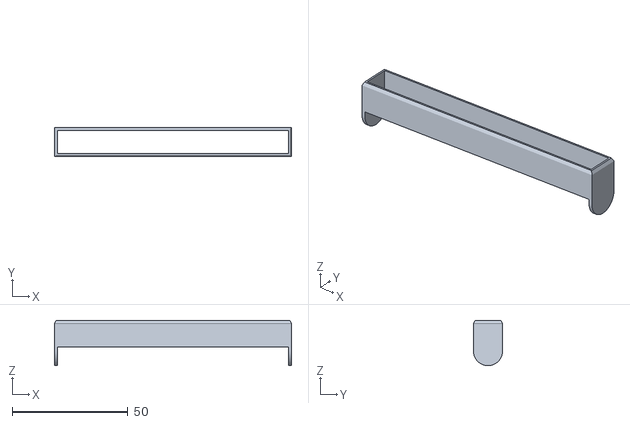
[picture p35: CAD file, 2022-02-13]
lack-enclosure-mods/mmu-ptfe-pass-insert.stl
102.6 x 12.6 x 19.6

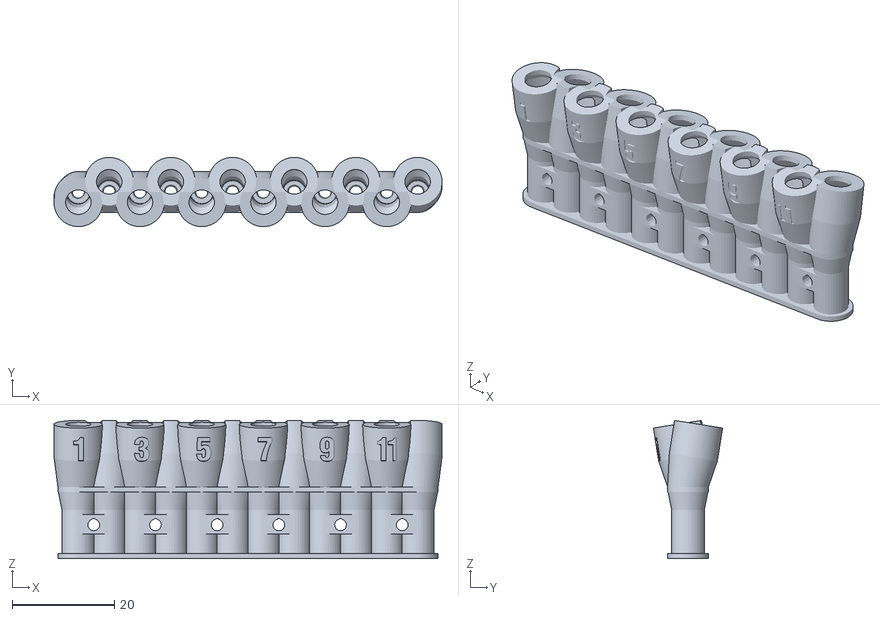
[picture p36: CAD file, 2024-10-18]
stl/v3.3/mmu12x-inlet.stl
75.7 x 13.5 x 27.0

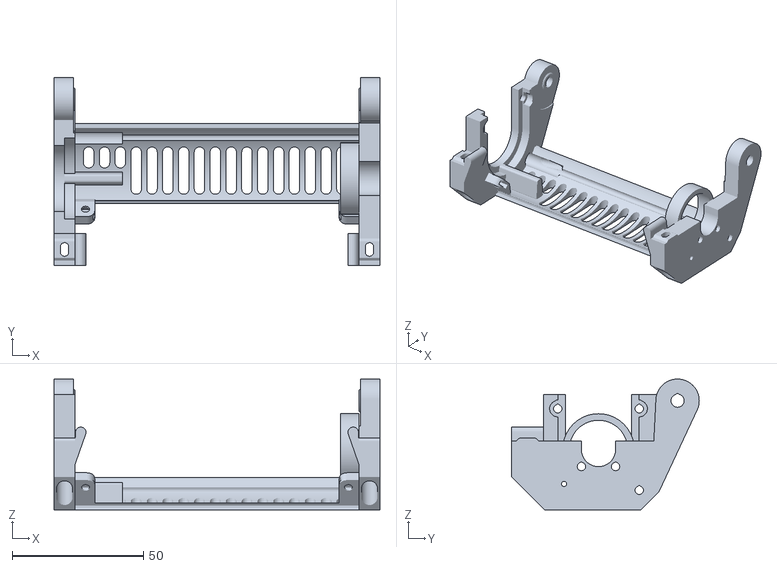
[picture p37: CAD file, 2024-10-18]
stl/v3.3/mmu12x-upper.stl
124.0 x 71.3 x 49.8

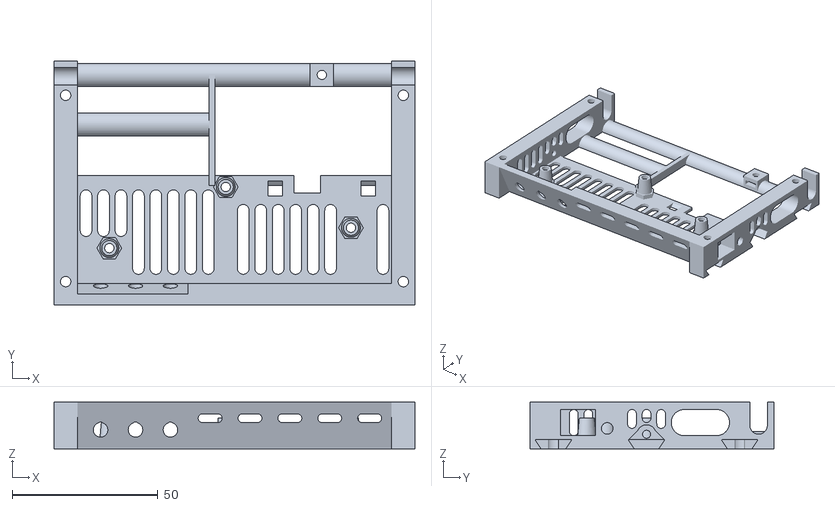
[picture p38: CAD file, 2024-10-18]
stl/v3.3/mmu12x-mcu.stl
124.0 x 83.8 x 16.0

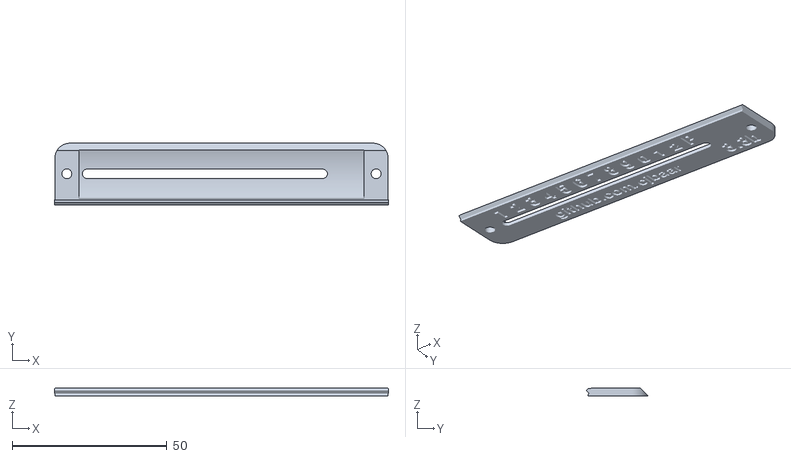
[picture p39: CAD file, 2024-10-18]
stl/v3.3/mmu12x-upper-panel.stl
108.0 x 19.9 x 2.50

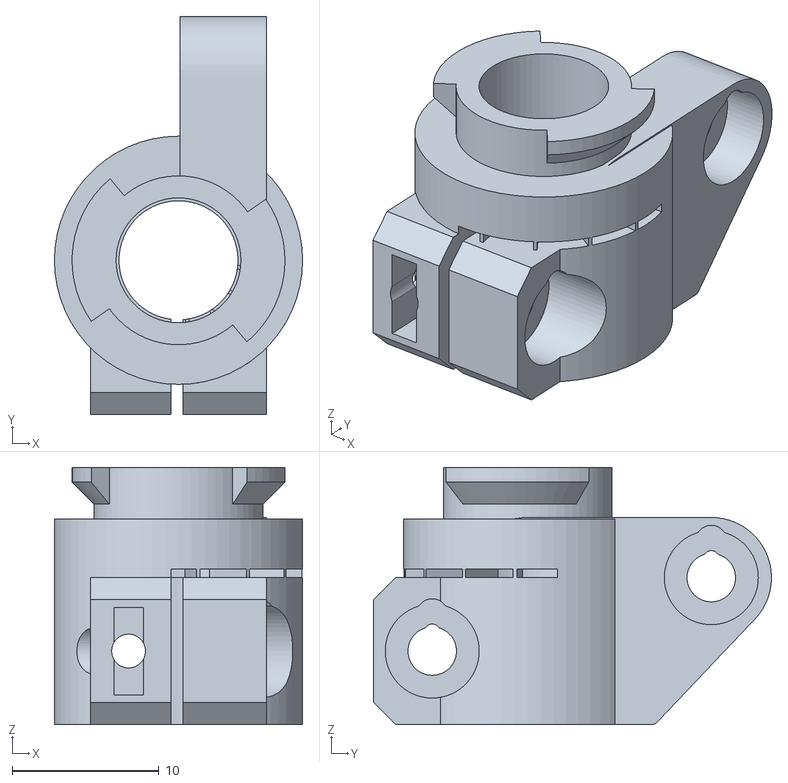
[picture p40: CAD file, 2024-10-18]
stl/v3.3/mmu12x-selector-plug.stl
16.9 x 27.1 x 17.5

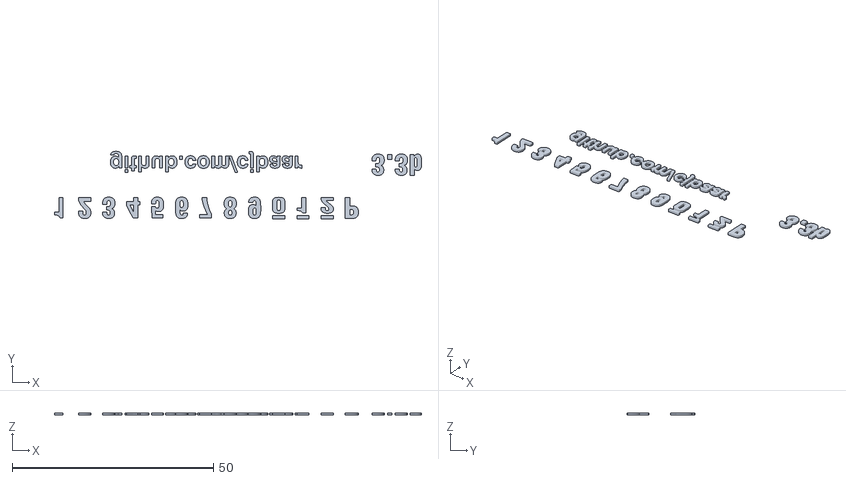
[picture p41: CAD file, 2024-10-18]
stl/v3.3/mmu12x-upper-color.stl
91.1 x 16.8 x 0.61

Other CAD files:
stl/v3.3/mmu12x-selector-2pc-m10.stl
stl/v3.3/mmu12x-idler-rings.stl
stl/v3.3/mmu12x-bracket-frame.stl
stl/v3.3/mmu12x-mcu-power.stl
stl/v1.4/mmu12x-bracket-frame.stl
stl/v1.4/mmu12x-bracket-table.stl
stl/v1.4/mmu12x-idler-ends.stl
stl/v1.4/mmu12x-idler-mount.stl
stl/v1.4/mmu12x-idler-rings.stl
stl/v1.4/mmu12x-mcu.stl
stl/v1.4/mmu12x-screen.stl
stl/v1.4/mmu12x-selector-2pc-m10.stl
stl/v1.4/mmu12x-selector-2pc-m6.stl
stl/v1.4/mmu12x-selector-plug.stl
stl/v1.4/mmu12x-upper.stl
stl/v1.4/mmu12x-wrench.stl
stl/v3.3/mmu12x-finda-wire-clip.stl
stl/v3.3/mmu12x-lower-mod.stl
stl/v3.3/mmu12x-selector-2pc-m6.stl

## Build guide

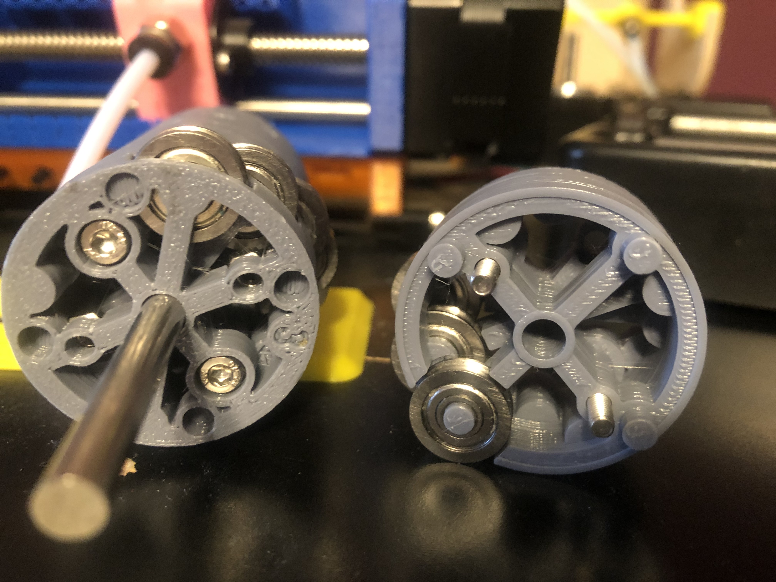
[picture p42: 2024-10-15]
img/idler-assembly.jpeg

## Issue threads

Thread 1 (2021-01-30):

design question

kml-pt, 2021-01-30:
Impressive project! What CAD platform did you use for the design? Would you be willing to share the CAD files? I would like to put different sized fittings on the inlet.

cjbaar, 2021-02-17:
Sorry, not currently prepared to share the source files. There are options for m6 and m10 fittings, and someone else did a mix for a push fitting like the original Prusa one uses. What fitting are you looking to use?

kml-pt, 2021-02-17:
I like to tap an unthreaded 4.2mm hole to use with m5 fittings. But I went ahead with your m10 design and liked it more than I thought I would.

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

cjbaar, 2021-02-17:
The m10 is definitely my favorite, as it lets me get the PTFE all the way up to the exit point, so IMO less risk of catching on the fitting itself. Another user made a re-mix of selector for 12x, but allows the use of the heat-set insert like Prusa used. See if this is what you are looking for. I haven't added it the repo yet.
[HeatSet-mmu12x-selector-v1.1.stl.zip](https://github.com/cjbaar/prusa-mmu-12x/files/5997583/HeatSet-mmu12x-selector-v1.1.stl.zip)

3d-gussner, 2024-10-24:
@cjbaar Do you plan to provide the cad files at some point? If not a problem, just asking before trying to convert the STL files to STEP or cad files manually.

cjbaar, 2024-10-24:
Sorry, not at this time. Is there something specific you are looking to modify?

3d-gussner, 2024-10-25:
> Sorry, not at this time. Is there something specific you are looking to modify?

No problem. I was looking at the STL files and the config changes you have made.
If I am not mistaken the idler bearings are 25° of each other but in the config.h you have 25.4° See https://github.com/cjbaar/Prusa-Firmware-MMU-12x/blob/main/src/config/config.h#L213

Maybe I didn't convert the STL correctly to a STEP/ Fusion360 and am there off by 0.4°

cjbaar, 2024-10-25:
They are 25.2° by design, but I found that 25.4° worked better in the code for proper alignment. Something about the motor steps, perhaps? It's a very small adjustment.

3d-gussner, 2024-10-28:
> They are 25.2° by design, but I found that 25.4° worked better in the code for proper alignment. Something about the motor steps, perhaps? It's a very small adjustment.

Calculating the degrees to actual steps is very hard. The NEMA has 200 Steps per rotation and so 1.8° per full step. With microsteps you get it better. The 32u4 has very limited resources and calculating floats isn't easy here.
Actually your 25.2° are "perfect" full steps (25.2/1.8=14) but you never know what the home position is and so the stepper is probably all the time in some microsteps.

3D printed parts + bearings + tolerances add up quickly and often the "perfect" 25.2° in CAD are in real world 25.4°

Closed 2022-12-31.

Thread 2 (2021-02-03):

Nice work, impressive

TheZeroBeast, 2021-02-03:
Hey mate,
Nice work, looks like a nice solution.

I'd like to discuss any issues you've faced in your journey with this mod.

Would be cool incorporating some of the software mods I've done to make the MMU2S more reliable.
https://github.com/TheZeroBeast/TZB-MMU2S-Firmware

cjbaar, 2021-02-17:
Thanks for sharing. My fork of the MMU code is so far off the original now, I doubt I will ever try to merge it back. I can't even get them to respond to the relatively small changes needed in the main printer firmware to support change codes over T4. I ended up taking out the eeprom stuff in my version. At the time I didn't feel like digging into the code there enough to understand it, and didn't want to mess with calibrating 12 filaments. Also needed every bit of program space to get the display running. Might look at it again later. In my case, I just adjust it by setting the value in the firmware that works for my PTFE length.

TBH, it never made much sense to me why I would need to calibrate every filament separately. They all through the same sensor, and the size of the selector and length of PTFE don't change.

TheZeroBeast, 2021-02-17:
Yeah, they don't seam to take on much of the assistance provided to them. I tried on a number of fronts for my code and hardware changes to MK3S parts I thought beneficial to the community and zero contact back.

My code only uses the one calibration length and then starts a synced sense portion that runs the MMU pulley synced with printer extruder to grab filament.

cjbaar, 2021-02-17:
Cool; I'll have to take a closer look at it. I pretty much re-wrote all of the load/unload and speed calculations from scratch. They had a lot off weird hard-coded numbers and break points in there, imo. One thing I did was slow down a lot more at the end, to try and match the speed I saw in the main firmware code. I did feel in the original MMU, final feed speed was still a fair amount faster than the extruder gears were running in "wait" mode, which created a higher risk of stripping, even with perfect length calibration. Sounds like that's the same idea you are working with.

flinke-flasche, 2021-04-15:
Really nice work. Thumb up.

I'm thinking about to print all parts and add them to my second Prusa MK3s.
On the first i have the original MMU2s.

Someday i have to use 12 colors in one print 😄

What are the differnces in both MMU2s firmware files you uploaded?

Why you don’t upload the changed Prusa Firmware for more then T4?

Thank you
Tobias

cjbaar, 2021-04-15:
For the MMU, one has the display integrated (SSD1306) one does not. For the one without display, the buttons use the original Prusa operating code.
I have uploaded a compiled .hex of the printer firmware with support for 12 filaments, but again, I have not tested uploading this. I hav only flashed using the Arduino IDE.

WarrenSchultz, 2021-04-15:
I've ordered the parts to give this a whirl (with display).
So, as I understand it, unless Prusa implements a major breaking change to the MMU2/MK3 firmware combination, I can use any stock or custom compiled firmware with your MMU2 firmware, as long as I make the tool changes necessary for the Mk3?

cjbaar, 2021-04-15:
@WarrenSchultz Yes; the printer firmware has relatively little changes. The biggest of which is that the original has a hard-coded cap of reading anything above T4. So if you want to patch another version, yes that should work. I was hoping someone would have looked at my PR by now, since it doesn't affect much.

The MMU firmware, however, was heavily modified, so I don't have a PR for that; you would need to use or branch from my fork.

WarrenSchultz, 2021-04-15:
I went and found the PR, looks like there are a couple conflicts now vs. when you did the initial PR, since they did a huge refactor since then. Maybe taking care of those will allow it to sail through? (Especially if those who are following this project boost it.)

I've looked at the MMU2 code before, and I don't have any interest in second-guessing your work on it :D

cjbaar, 2021-04-15:
I can see that conflicts exist; can't see easily what they are. Looks some changes to menus? Maybe they moved to loops like I did, instead of hard-coding 1-5. Realistically, you could make the changes to Marlin code to accept T>5 and that would be enough. The menu changes are only necessary if you ever use the "Load filment X" which I never do. When not printing multi-color, I usually just disconnected my MMU

flinke-flasche, 2021-04-16:
> I've ordered the parts to give this a whirl (with display).
>
> So, as I understand it, unless Prusa implements a major breaking change to the MMU2/MK3 firmware combination, I can use any stock or custom compiled firmware with your MMU2 firmware, as long as I make the tool changes necessary for the Mk3?

Where do you ordered the parts?
Could you order everything in one shop?

zonkie, 2021-04-16:
Guys this is so awesome! I read about this and i follow your discussion actively. I'm not yet sure, if i want to rip my mmu2s apart, but if you get this running, i think i might give it a shot. Maybe we can try to implement the mk3 firmware changes in a configurable way, so Pruša might accept the pull request (unlikely, but worth a shot ;).

cjbaar, 2021-04-16:
@flinke-flasche Pretty sure I just got all the "additional" parts on Amazon, but has to use most of the parts from the stock Prusa unit. If you try to source everything from scratch, I could not find anywhere to buy things like the Prusa custom motors (w/ 100m shaft or screw). Also, I have seen knockoff control boards, but someone else I know that bought one said it didn't work right with the firmware. So, basically, I am not aware my 12x unit can be built unless you already bought the Prusa one. Happy to hear if anyone else has success otherwise.

cjbaar, 2021-04-16:
Just curious... where are people finding or hearing about this build? Never really expected so much interest in it :)

WarrenSchultz, 2021-04-16:
> Just curious... where are people finding or hearing about this build? Never really expected so much interest in it :)

I stumbled onto it a while back, I can't remember where, and forgot about it. Then I saw that TZB had commented on it (whose firmware for the MMU2/Mk3 I use/follow on github), and I remembered I wanted to investigate further. I've been perpetually annoyed by the MMU not having its own display for error codes, and that alone was enough for me to be interested.

zonkie, 2021-04-16:
I cant remember where, i was looking for a color change within a toolhead in the mmu2 and found this... I believe it was mentioned in the Pruša forums.

flinke-flasche, 2021-04-16:
I think someone posted it in a facbook group because of the  presentation of the palette 3.

cjbaar, 2021-04-16:
@WarrenSchultz So, I never tested this because I ripped my MMU apart, but if you just want the screen and error-handling I wrote, you *should* be able to use my MMU firmware with the stock Prusa model. I tried to write everything with parameters, so the motor directions, steps, etc. all are configurable. If you want to try it out, you can compile with the "prusa-mmu2s-display.h" config file

flinke-flasche, 2021-04-19:
> @flinke-flasche Pretty sure I just got all the "additional" parts on Amazon, but has to use most of the parts from the stock Prusa unit. If you try to source everything from scratch, I could not find anywhere to buy things like the Prusa custom motors (w/ 100m shaft or screw). Also, I have seen knockoff control boards, but someone else I know that bought one said it didn't work right with the firmware. So, basically, I am not aware my 12x unit can be built unless you already bought the Prusa one. Happy to hear if anyone else has success otherwise.

I would like to test your build with a MMU2 from AliExpress, especially this one

https://a.aliexpress.com/_veXkkR

cjbaar, 2021-04-19:
@flinke-flasche That's interesting. I didn't full knock-offs like this existed, though I guess I shouldn't be surprised. I am interested in knowing how that turns out, especially with regard to the MCU board.

zonkie, 2021-05-23:
Alright, as this looks like it's working, i started printing the parts. I'm still hesitant about disassembling the original one, but when i oder a knockoff, im having the original one flying around without any use... So I'm probably going that route. Still have some time to decide, the prints will there their time ;)

Is one 1kh roll of PETG enough?

flinke-flasche, 2021-05-23:
@zonkie
1kg ist enough.

i thought i will buy a copy from Aliexpress but then i disassembled the original one.
If you have a lot of screws and nuts you don't have to disassembling the complete MMU2. The only thing is that you have to cut the brass tubes. But with 5 mm less you can use it in your original as well.

cjbaar, 2021-05-26:
@zonkie According to Prusa Slic3r, all the printed parts should be somewhere around 250g total.

Mirarkitty, 2021-12-28:
Very nice work. I'd like to build one of those... how did the aliexpress build work out?

As for calibrating every filament, it's to calibrate every idler. From when it was super sensitive on the millimeter that it would hit the idler of the extruder, and MMU idler diameter differences were enough to make it unstable. No longer needed - now triggering on the sensor of the extruder instead...

Johnday29, 2022-04-01:
Is this still an active project?  Have you updated it to work with any of the current firmware or slicer?

cjbaar, 2022-04-01:
I have not done anything with the printer firmware since 3.9. It's just a matter of allowing the g-code interpreter to pass through tool values above T4, but I haven't had a reason to upgrade.
There should no be issues with any version of slicer; you just have to create a printer profile with more extruders.

Johnday29, 2022-04-01:
Awesome, build my unit as we speak!

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

Johnday29, 2022-04-02:
So I can't find the STL for the Idler cylinder  am I blind or is it missing?

cjbaar, 2022-04-02:
In my design, that part is the most different from the original. It's not one piece, it has to be assembled. Print one idler end, one mount, and 4x the idler-rings

cjbaar, 2024-10-18:
This project has been updated for the MMU3+Mk4. Please check the readme files for further info.

Johnday29, 2024-10-18:
Yes! If this works I will definitely be donating to the project. Thanks.

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

Closed 2024-10-18.

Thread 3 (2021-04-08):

Looks like fun project

rmilyard, 2021-04-08:
I have bunch extra MMU2 parts and was looking for something like this to undertake.  Just wondering if have more detail build or guide yet?

rmilyard, 2021-04-09:
Looking for info as how wire in OLED also

Huang-TS, 2021-04-10:
I can't wait to watch some demo video about this nice project.

rmilyard, 2021-04-11:
I am working on prints now.  Using PLA CF.

Closed 2022-12-31.

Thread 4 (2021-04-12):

Compile MMU2S code

rmilyard, 2021-04-12:
I am trying to figure out how to compile the code.  I am not sure I understand how to do this.

Arduino: 1.8.5 (Windows 10), Board: "Original Prusa i3 MK3 Multi Material 2.0 upgrade"

Build options changed, rebuilding all
C:\Users\rmily\Desktop\MM-control-01-master\MM-control-01-master\MM-control-01\version.ino:13:10: fatal error: dirty.h: No such file or directory

 #include "dirty.h"

          ^~~~~~~~~

compilation terminated.

exit status 1
Error compiling for board Original Prusa i3 MK3 Multi Material 2.0 upgrade.

This report would have more information with
"Show verbose output during compilation"
option enabled in File -> Preferences.

Panayiotis-git, 2021-04-12:
create a new dirty.h file (next to the main.h) with content:
#define FW_LOCAL_CHANGES 0

rmilyard, 2021-04-12:
Thanks.  I made that file and now getting this error.  I am noob when codes to compiling firmware sorry.

Arduino: 1.8.5 (Windows 10), Board: "Original Prusa i3 MK3 Multi Material 2.0 upgrade"

In file included from sketch\main.cpp:20:0:

version.h:7: error: stray '$' in program

 static const uint16_t fw_buildnr = ${GIT_PARENT_COMMITS}; //!< number of commits preceeding current HEAD

                                    ^

In file included from sketch\main.cpp:20:0:

version.h:7: error: 'GIT_PARENT_COMMITS' was not declared in this scope

 static const uint16_t fw_buildnr = ${GIT_PARENT_COMMITS}; //!< number of commits preceeding current HEAD

                                      ^~~~~~~~~~~~~~~~~~

exit status 1
stray '$' in program

This report would have more information with
"Show verbose output during compilation"
option enabled in File -> Preferences.

rmilyard, 2021-04-13:
Well I have been messing with this 3 day now and just can't seem to get it compiled.

cjbaar, 2021-04-13:
So this is based on the Prusa repo, which uses Arduino to compile. It can be a lot if you are unfamiliar with Arduino and the IDE. The full build docs from https://github.com/prusa3d/MM-control-01 may help. Part of the process is you have to create your own version.h. I am using the following values. They don't mean much, but they have to be above certain versions for the printer firmware to accept communication.
```
static const uint16_t fw_version = 111; //!< example: 103 means version 1.0.3
static const uint16_t fw_buildnr = 505; //!< number of commits preceeding current HEAD

cjbaar, 2021-04-13:
My whole IDE is messed up right now because I made the mistake of updating and Arduino steps on its own libraries/avr, so I can't get 1.8.5 to work now. When I can get a working env, I can try creating a .hex file for direct upload, but right now I don't have a runtime method to alter the PFTE length.

rmilyard, 2021-04-13:
Thanks.  Right now I am getting these errors when changing per above:

Arduino: 1.8.5 (Windows 10), Board: "Original Prusa i3 MK3 Multi Material 2.0 upgrade"

Archiving built core (caching) in: C:\Users\rmily\AppData\Local\Temp\arduino_cache_507581\core\core_PrusaResearch_avr_prusa_mm_control_7808ed4679fb9bf84d9889cab7737b64.a
C:\Users\rmily\AppData\Local\Temp\ccqG87OG.ltrans0.ltrans.o: In function `tmc2130_rx':

sketch/tmc2130.c:320: undefined reference to `tmc2130_cs_low'

sketch/tmc2130.c:321: undefined reference to `spi_txrx'

sketch/tmc2130.c:322: undefined reference to `spi_txrx'

sketch/tmc2130.c:323: undefined reference to `spi_txrx'

sketch/tmc2130.c:324: undefined reference to `spi_txrx'

sketch/tmc2130.c:325: undefined reference to `spi_txrx'

sketch/tmc2130.c:326: undefined reference to `tmc2130_cs_high'

sketch/tmc2130.c:330: undefined reference to `tmc2130_cs_low'

sketch/tmc2130.c:331: undefined reference to `spi_txrx'

sketch/tmc2130.c:333: undefined reference to `spi_txrx'

sketch/tmc2130.c:334: undefined reference to `spi_txrx'

sketch/tmc2130.c:335: undefined reference to `spi_txrx'

sketch/tmc2130.c:336: undefined reference to `spi_txrx'

sketch/tmc2130.c:337: undefined reference to `tmc2130_cs_high'

C:\Users\rmily\AppData\Local\Temp\ccqG87OG.ltrans0.ltrans.o: In function `tmc2130_tx':

sketch/tmc2130.c:306: undefined reference to `tmc2130_cs_low'

sketch/tmc2130.c:307: undefined reference to `spi_txrx'

sketch/tmc2130.c:308: undefined reference to `spi_txrx'

sketch/tmc2130.c:309: undefined reference to `spi_txrx'

sketch/tmc2130.c:310: undefined reference to `spi_txrx'

sketch/tmc2130.c:311: undefined reference to `spi_txrx'

sketch/tmc2130.c:312: undefined reference to `tmc2130_cs_high'

C:\Users\rmily\AppData\Local\Temp\ccqG87OG.ltrans0.ltrans.o: In function `tmc2130_init_axis_current_normal':

sketch/tmc2130.c:218: undefined reference to `__res'

C:\Users\rmily\AppData\Local\Temp\ccqG87OG.ltrans0.ltrans.o: In function `tmc2130_init_axis_current_stealth':

sketch/tmc2130.c:205: undefined reference to `__res'

C:\Users\rmily\AppData\Local\Temp\ccqG87OG.ltrans0.ltrans.o: In function `tmc2130_init':

sketch/tmc2130.c:247: undefined reference to `selector_step_pin_init'

sketch/tmc2130.c:248: undefined reference to `pulley_step_pin_init'

sketch/tmc2130.c:249: undefined reference to `idler_step_pin_init'

sketch/tmc2130.c:250: undefined reference to `selector_step_pin_reset'

sketch/tmc2130.c:251: undefined reference to `pulley_step_pin_reset'

sketch/tmc2130.c:252: undefined reference to `idler_step_pin_reset'

collect2.exe: error: ld returned 1 exit status

exit status 1
Error compiling for board Original Prusa i3 MK3 Multi Material 2.0 upgrade.

This report would have more information with
"Show verbose output during compilation"
option enabled in File -> Preferences.

cjbaar, 2021-04-13:
Yeah I am getting that, too. These files come straight from the original, and I haven't touched them since last successful compile. I think it's because, like I said, I updated the IDE, and now the AVR is showing as v7.3.0, and probably has a different core now. Not sure how to revert the back-end without wipe and re-install.

cjbaar, 2021-04-13:
Yeah, this is really frustrating. I can get it to compile on an older laptop with an untouched install of 1.8.5, which is using avr-gcc v5.4.0. Unfortunately, IMO, the Ardiuno IDE does not deal with upgrades and libraries/sketches that compiled fine under certain avr versions. I still have a copy of 1.6.11 because I have a sketch that breaks serial communication with any other version.

cjbaar, 2021-04-13:
I add compiled .hex files to this repo. However, I *have not tested them*. Use at your own risk.

rmilyard, 2021-04-13:
Ok.  I have all part pretty much printed.  Still trying to figure out how all goes together but hope to test soon!

rmilyard, 2021-04-14:
Do you have anymore build info?  I am trying to figure out how mounted idler in the upper part.

cjbaar, 2021-04-14:
Currently I don't; actually wasn't expecting this to catch on. :) It mostly assumes you previously built the Prusa model, and most of the design is similar. For the idler, you assemble the 14 pieces on a 5mm shaft. Repeat the 1/2/3 pattern (# printed on bottom), and you can optionally embed m3 screws to keep it tight as you go (every 3 rings). The oval piece holds the bearing, and mounts to the top with two m3 screws.

rmilyard, 2021-04-15:
I have few questions maybe if don’t mind can email me so can get this built. I am willing to help any way I can.   My email is rmilyard@hotmail.com

cjbaar, 2021-04-15:
Sorry @rmilyard, looks like hotmail is blocking IP ranges from my mail host. Do you have another address? Otherwise, ask here and I will do what I can to help.

rmilyard, 2021-04-15:
rmilyard@gmail.com and rmilyard@cox.net

cjbaar, 2021-04-15:
@rmilyard I added a few more pics under [https://github.com/cjbaar/prusa-mmu-12x/blob/master/TIPS.md](https://github.com/cjbaar/prusa-mmu-12x/blob/master/TIPS.md) with some additional assembly tips. Hope this helps.

rmilyard, 2021-04-15:
Ah. So like this?

[cid:08121F0B-0515-488F-BCD7-74189DE612AB]

[cid:82D47372-7244-432D-B3FE-30042E4BFD3B]

Sent from my iPhone

On Apr 15, 2021, at 3:25 PM, cjbaar ***@***.***> wrote:

@rmilyard<https://github.com/rmilyard> I added a few more pics under https://github.com/cjbaar/prusa-mmu-12x/blob/master/TIPS.md with some additional assembly tips. Hope this helps.

—
You are receiving this because you were mentioned.
Reply to this email directly, view it on GitHub<https://github.com/cjbaar/prusa-mmu-12x/issues/4#issuecomment-820766574>, or unsubscribe<https://github.com/notifications/unsubscribe-auth/ACUT57QAGP2VAWPX3RFOAMDTI5RVPANCNFSM42ZY6Y2A>.

cjbaar, 2021-04-16:
Sorry I don't see any images with that post; just some sort of id ref.

cjbaar, 2021-04-19:
@rmilyard I did upload some compiled .hex files, but based on my testing, PrusaSlic3r will not uploaded it properly. It is not recognizing it as being for the MMU, and so is trying to use the avr settings for the einsy instead. I am not sure what PrusaSlic3r uses to determine this.

cjbaar, 2021-04-19:
@rmilyard OK; it helps to read the docs. :) I had to manually add a comment to the beginning of the hex files to be recognized as being for the MMU. I did some brief testing, and was able to upload the included .hex files to the MMU using PrusaSlic3r.

flinke-flasche, 2021-04-23:
That sounds good. Did you print a test if the MMU works well with your firmware?

Whats about the firmware for the MK3+? did it work as well?

zonkie, 2021-06-11:
I flashed your Files yesterday and assembled everything, but as soon as the printer wants to start Printing, it Resets itself. After the reset, the printer does the bed leveling procedure, and the MMU cries that it has a homing error, because the Filament ist still loaded... Did i mess up the wiring there, or is this some kind of Safety feature in the Printers firmware?

zonkie, 2021-06-11:
I think, this ist some security mechanism of the printer. It checks, is the file was sliced for the Pruša and if not, it resets.

Also the idler positions itself at the wrong direction, for me. But i have to wait for two u-bearings anyway, gonna disassemble it again then ;(

cjbaar, 2021-06-13:
Don't think I have run into the reset issue before. Are you using something other than Prusa Slic3r for slicing? Not that the printer should care.
Can you describe more what you mean by "the idler positions itself at the wrong direction?" As I mentioned in the notes, I tried using the motor feedback for homing, but it doesn't always work well. If it is not resetting all the way back, you could try manually moving it to the end before turning on.

zonkie, 2021-06-13:
Yes i used m existing prusa profiles on prusaslicer (only added some extruders :) ). I also created a custom profile with the settings from the original one.
I read in the Prusa Forums that this might be a mechanism that happens if the code was sliced for a different printer...

For the idler positioning... well, it seems, that when starting the print, it first selects the correct feed line, but before loading, it turns the idler from e.G. Position 3 to 2, but the output selector stays at 3. I can see the dot for number 2 at the top slit, so it seems not to happen accidental but is precisely positioned. I'm still waiting for two more u-bearings, so i have to take it apart again anyway. I will see of i can adjust something then.

Also ill try to flash all firmwares again, just to rule out that i have flashed maybe the original firmware or so...

zonkie, 2021-06-14:
So here is another case in the prusa forum, he is also having the issue with the wrong slot loaded in the MMU. So it seems to be an issue with the original mmu and mk2s firmwares too. I'll try to adjust the filament probes as soon as i have time for it, as this might be the issue in some cases there.

https://forum.prusaprinters.org/forum/original-prusa-i3-mmu2s-mmu2-assembly-and-first-prints-troubleshooting/i3-mk3s-mmu2s-rebooting-at-print-start/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

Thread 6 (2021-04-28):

Attach Upper and Lower

rmilyard, 2021-04-28:
What did you use here to mount these together?

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

cjbaar, 2021-04-28:
Sorry @rmilyard my email responses to you are being blocked by Hotmail for some reason. I used M5 screws, which should thread loosely into the hole on the upper piece. You could also try the 5mm pins from the original, but they might be too tight.

Closed 2022-12-31.

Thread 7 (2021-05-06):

Powered on.

rmilyard, 2021-05-06:
So I plugged it all in as would MMU2S.  I flashed both firmware.  I am not seeing it.  I see light on MMU2 board but MK3S not seeing MMU2 connnected.

rmilyard, 2021-05-11:
Nope never got working

cjbaar, 2021-05-13:
Sorry I don't have access to the boards right now. I tried the firmware I uploaded, and have the same issue. The MMU boots, but printer does not see it. Not sure what needs to be changed, but for the moment I am afraid that you will need to be able to compile this locally on Arduino 1.8.5 to upload.

rmilyard, 2021-05-13:
That sucks!  I have it completely built but like said isn't seen my printer.

flinke-flasche, 2021-05-14:
@rmilyard
Have you tried to print something with the new firmware without the MMU2? Does it work?

@cjbaar
Maybe something is missing in one of the firmwares?
The MK3s have to know that a MMU2 is connected and the MMU2 have to say “hello MK3s, here i am. Please unlock the menu.“.

At the beginning of printing with the MMU2, i had the same issue. The MK3s didn't saw my MMU2 several times.
This was before the 1.6 firmware was launched.
I had to resart the MK3s several times till it recognize the MMU2.

rmilyard, 2021-05-15:
Got it all loaded.  I will play with it more tomorrow.  How tight use have idler screws?

flinke-flasche, 2021-05-18:
@rmilyard
any news yet?

My last parts arrived today. now i'm ready the transform my MMU2 in a MMU12x :-)

rmilyard, 2021-05-18:
@flinke-flasche  I was able to get it to boot up.  I haven't had time to mess with it.  First try I couldn't get filament to load yet.

flinke-flasche, 2021-05-22:
I set up my MMU12x. Everything works perfectly. I love it and it looks much better as the MMU2 :-)

@rmilyard do you think you can compile a multi language Firmware for the MK3s? i'm from Germany :-)

I use Octoprint for my Printers. Octoprint can't use only 10 Extruders. i do a feature request to Octoprint.

cjbaar, 2021-05-26:
The MK3 firmware includes files for multi-language compilation, though I have not tried using them before. Unfortunately, at the moment, I have not put similar adjustments in the MMU display code.

As far as octoprint limiting filaments, I had similar issue with Prusa, which is why I had to modify the MK3 firmware as well. Not sure why these systems have so much hard-coding; it should literally just be forwarding on whatever you find in the g-code.

cjbaar, 2021-05-26:
@rmilyard I only tighten my idler screws a couple of turns. I don't think it needs as much pressure as the original, but your results may vary.

flinke-flasche, 2021-05-30:
@cjbaar
do you think you can compile the Firmware with multilanguage?

Maybe you can add a post at my Octoprint request.
https://github.com/OctoPrint/OctoPrint/issues/4149

Can you tell me what the tiny numbers under the selected filament at the display is showing?

cjbaar, 2021-06-03:
1) I don't have a working Arduino IDE 1.8.5 right now. I need to get something working again to compile these.
2) What is the issue with OctoPrint? I haven't used it much. Is it only sending G0-G9, so the last two filaments end up repeating filament color #10?
3) The numbers show total load/unload attempts and failures. Describe on the FW page: https://github.com/cjbaar/MM-control-01

zonkie, 2021-06-04:
I think it's just the Max-Value in the HTML5 Field in the template. I could just put in 12 and send it, and it saved :)

I haven't got my MMU Working as i'm waiting for Parts, so i couldn't try it out, but otherwise i'd open a pull request for that change in OctoPrint and also in the MMU2S Filament Selector Plugin.

flinke-flasche, 2021-06-06:
@zonkie
You’re right. I can type it manually in the field and then it works perfectly.
I’ve tested it today.

bist du auch aus Deutschland?

@cjbaar
No more octoprint problems.
thank you for the display description.

i love your MMU12x.
thank you for sharing.
The firmware works perfectly for me.

zonkie, 2021-06-06:
I'm still waiting for parts... An m3 screw set and 10 of the 12 ordered u-shaped-bearings have arrived yet (thanks, ebay-seller, the bag is even labeled with "12pcs"...) Also some of the AliExpress things seem to have arrived in Germany, waiting for customs :) also i'm printing lots of spool-holders...

@flinke-flasche yes, i live near Hamburg :)

Closed 2024-10-18.

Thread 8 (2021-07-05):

Stuck in tool change 1

Prusaprinter44, 2021-07-05:
Installed and updated both firmwares. The print is stuck on tool change 1 and just freezes over the purge block. Running MMU board firmware without screen.

zonkie, 2021-07-06:
Try helping it with the filament change, for me it was usually that it didn't recognize the filamemt was ejected, when this error occured.

Obel1sk, 2021-07-06:
I use a lot of PETG and can get a lot of stringing until I get the temps dialed in for each roll. When the display reports an UnLoad failure, I unscrew the PTFE connector and push the filament out the front of the selector*, clip the string and manually position the filament back to the load position**, press "OK" on the display interface and the MMU will re-cycle and re-detect the filament, clearing the error and completing the unload.

* I use the "original m5 heat-set remix" so as not to wear out the plastic threads.
** replace the PTFE connector

cjbaar, 2021-07-06:
If you compiled without the screen, then the MMU LEDs should serve as indicators just as they did before, just any filament over #5 will show as LED #5, I believe. Without more info, I am guessing one of the filament sensors needs alignment. What does the printer show? Is the extruder motor still moving? Did the filament unload? Not sure what "stuck" means.

Prusaprinter44, 2021-07-11:
The filaments all load to nozzle and it appears the issue is happening at
the bondtech area in the extruder, it retracts to just above the gear and
the mmu itself is not retracting the filament beyond that point.  All of
the sensors are working, I am thinking it may be in the U channel bearing
as i have noticed there are 2 versions of bearings, 1 with a deeper groove
and 1 with a less pronounced groove in the bearing, i have tried both
versions with the same result, can anyone send some screen shots of the
tension springs? It seems much different then the regular mmu, we currently
run 12 five color mmus without any issues so tuning this shouldn't be a
problem.

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

flinke-flasche, 2021-07-12:
How long is your PTFE tube?
Did you calibrate the PTFE length?

I had problems after I calibrated the PTFE length.
After resetting the MMU and flashing the firmware everything works fine.

Prusaprinter44, 2021-07-13:
I have gone back and forth between the stock length and a few mms longer, This may sound silly but does this setup require the Bowden tube calibration like it did in the past? My current length on the bowden tube is 14.17 " or 359 mm.  Using a m6 fitting on the selector and m10 on the IR sensor.

I think I have narrowed it down to spring tension on top or a bowden length issue. All of the commands work fine manually, the problem occurs when it wants to unload.

cjbaar, 2021-07-14:
So in the interest of space, and my lack of understanding of Prusa's use of eeprom storage, my code disabled all of the length calibration. You just need to enter the length (in mm) in your config.h when compiling if it's not the same as the stock Prusa PTFE. I doubt any of that would affect MMU functions though. On load, the MMU will stop as soon as the filament hits the extruder, you just might get a bit of grinding if it is set too short. If it is set too long, the printer will ask for "C0" (continue) so the filament would eventually get there anyway. During unload, the length only comes into play during the last part (as it approaches the FINDA). If the MMU isn't retracting, it's because the printer is not telling it to. The MMU is pretty dumb in comparison to the printer firmware, and generally only does what it's told. The screen would help debug (as it outputs the last command received), but if it not making any attempt to retract, then I would really lean toward the filament sensor on the extruder being misaligned.

Closed 2024-10-18.

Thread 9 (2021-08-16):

mmu12x-inlet is not a manifold

KaruroChori, 2021-08-16:
Trying to slice mmu12x-inlet in cura will result in visible holes on top of the geometry.
SuperSlicer with a similar profile is able to repair the mesh before slicing.

cjbaar, 2021-08-16:
PrusaSlic3r tells me "Auro-repaired 10 errors." The top gets a bit odd with the slight angle on the threads, but I have printed the part several times without issue.

KaruroChori, 2021-08-16:
Yes, same as with SuperSlicer; as they are both forks of Slic3r it does make sense I guess.
I was able to print it just as you said, which is why I had closed this issue.

Btw, thank you for sharing. It is going to be a lot of fun!

Closed 2021-08-16.

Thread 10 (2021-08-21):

Firmware compiling

flinke-flasche, 2021-08-21:
Does anyone have compile the actual firmware for using the Super PINDA?

cjbaar, 2021-08-21:
I wasn't aware they changed the sensor. It looks like it says it requires 3.9.2 or higher, and my mmux12 was forked at 3.9.0. Since they don't seem to have any interest in merging my changes, the mods will have to be re-done. I might try to work on a patch for future version, but am not able to do it for a while.

flinke-flasche, 2021-08-25:
The MK3S+ got this new sensor.
It's not really necessary right now. I can install it on my second prusa.
But if the sensor is really better than the old one, i want to install it on the prusa with the mmu12x.

flinke-flasche, 2021-10-30:
Thank you.
Works fine.

VSCustoms, 2021-11-03:
Hi corn62.

 I am still fairly new to VSCode so I have not completely figured out where to make all the changes. Would you be able to compile it for a MK2.5s with RAMBo13a board?

 I cant seem to find where I make the changes in the Marlin_main.cpp area.

corn62, 2021-11-03:
To be fair I am far from being an expert myself.
I just went down the changes initially made by the author (https://github.com/prusa3d/Prusa-Firmware/compare/MK3...cjbaar:MK3) and apply them all to the latest Prusa Firmware available on Github.
Then compiled everything following Prusa's guidelines.

Both files (3.9.0 and 3.10.0) were almost the same, I have no idea what it would look like for the MK2.5s.

VSCustoms, 2022-12-21:
>

I finally got a MK3S+ to try your firmwear out on. When loaded does it say MMU NA? did you happen to update yours to the new firmwear? just trying to get it all set up before I test print.

cjbaar, 2022-12-22:
@VSCustoms No, I haven't touched the printer firmware since 3.9.something. I think you have to set some version vars in one of the config files of the MMU code. It should not say "N/A" it should show the version connected.

cjbaar, 2022-12-31:
I have updated release 3.11.0 with the necessary changes for tools above T4. It is on my fork of PrusaFirmware, and there is a compiled MK3S version in the firmware folder of this repo.

Closed 2022-12-31.

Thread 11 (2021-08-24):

Custom Firmware for MK2.5s?

VSCustoms, 2021-08-24:
I’m just wondering if anyone has done custom firmware for the MK2.5s? I ordered everything to do this and then realized the firmware was just MK3s.

VSCustoms, 2021-11-01:
Ok I seem to be a little lost as I am unsure what I need to change now. I`m running 3.10.0 but I need your mods compiled for a MK2.5S vs a MK3S. Just not exactly sure what I`m changing. I`m still learning VScode.

VSCustoms, 2021-11-01:
Also I’m not worried about single mode settings as I never slice using that. I just pick my colour and if it’s only one I do that and print. I just need to be able to run 12 colours VS 5 if at all possible.

cjbaar, 2021-11-01:
Here are the changes I made in 3.9. You don't really need the AutoDeplete stuff if you don't use it, but you need the change in Marlin.cpp that recognizes codes above T4, and some of the stuff in mmu.h/mmu.cpp that relays those codes. The lcd changes make things print prettier, but may not be necessary. It's mostly about getting around the fact that they hard-coded only T0-T4 as acceptable values.

VSCustoms, 2021-11-23:
Ok I have finally figured out how to make it for a MK2.5s but I'm getting an error in the ultralcd.cpp file in arduino saying

 invalid conversion from 'const char*' to 'char' -fpermissive

Closed 2021-12-15.

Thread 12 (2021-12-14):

Compiling issue

VSCustoms, 2021-12-14:
Ok I got firmware 3.9.0 to compile and made a .hex file for my MK2.5s

My issue is when I redid everything to try and get 3.10.0 to work I get this .

C:\Users\Tim\AppData\Local\Temp\ccy70zps.ltrans0.ltrans.o: In function `process_commands()':

ccy70zps.ltrans0.o:(.text+0x5040): undefined reference to `mmu_filament_count'

C:\Users\Tim\AppData\Local\Temp\ccy70zps.ltrans25.ltrans.o: In function `Config_StoreSettings()':

ccy70zps.ltrans25.o:(.text+0x588): undefined reference to `mmu_filament_count'

C:\Users\Tim\AppData\Local\Temp\ccy70zps.ltrans25.ltrans.o: In function `ad_getAlternative(unsigned char)':

ccy70zps.ltrans25.o:(.text.unlikely+0x23e): undefined reference to `mmu_filament_count'

C:\Users\Tim\AppData\Local\Temp\ccy70zps.ltrans5.ltrans.o: In function `mmu_loop()':

ccy70zps.ltrans5.o:(.text+0x10ae): undefined reference to `mmu_filament_count'

ccy70zps.ltrans5.o:(.text+0x12e6): undefined reference to `mmu_filament_count'

C:\Users\Tim\AppData\Local\Temp\ccy70zps.ltrans19.ltrans.o:C:\Users\Tim\AppData\Local\Temp\arduino_build_755722\sketch/ultralcd.cpp:6240: more undefined references to `mmu_filament_count' follow

collect2.exe: error: ld returned 1 exit status

exit status 1
Error compiling for board PrusaResearch EINSY RAMBo.

Prusaprinter44, 2022-03-23:
Did you ever get this up and running on the 2.5s. I'm giving this a go again on a few of my machines.

VSCustoms, 2022-12-08:
>

Not sure how I missed this message. Unfortunately I did not get it working. It fought me the whole way and I needed my MMU up and running. I just recently got a MK3S+ I will be tackling it again on as I really would love to have the 12 colour option and I have been playing with VS code more maybe the 2.5S board did not like the custom farmwear.

cjbaar, 2024-10-18:
Closing this, as this project has moved on to MMU3+Mk4, which does not use the old compiler process.

Closed 2024-10-18.

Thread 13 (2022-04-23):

Tip Forming

Johnday29, 2022-04-23:
I have completed the setup and the filaments all seem to be on track and functioning.  The problem I am having is the tips don't seem to be forming correctly and are fat causing them to get stuck in the extruder and not retract into the mmu2s unit to allow it to switch to the next color.  do we need to adjust any settings on the tip forming or raming? Thanks

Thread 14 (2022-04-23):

Updated firmware please!!

Johnday29, 2022-04-23:
Any chance of getting new firmware with the update to fix the max T4?  The current firmware keeps crashing on my printer saying that the bed had temp issues even though the temp was just fine!

cjbaar, 2022-12-31:
I have updated release 3.11.0 with the necessary changes for tools above T4. It is on my fork of PrusaFirmware, and there is a compiled MK3S version in the firmware folder of this repo.

Johnday29, 2022-12-31:
Thank you so much!

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

Closed 2022-12-31.

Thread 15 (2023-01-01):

Question About Print Material

sabaatworld, 2023-01-01:
Thank you for keeping the project alive. I'm thinking of building this and was wondering if you would still recommend PLA as material of choice, based on your long term experience with your setup?

cjbaar, 2023-01-02:
I printed everything in PLA. Others have used PETG, but not sure if you would find the tolerances different.

grzlus, 2024-03-06:
PLA works fine. I printed a lot with it and it just works.

Closed 2024-09-30.

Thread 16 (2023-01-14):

MMU FW UPDATE NEEDED

grzlus, 2023-01-14:
I built and flashed both MMU and printer. For printer I used my own compiled software, as I have installed Mosquito Magnum with SliceEngeenering thermistor. Now I'm getting error `MMU FW UPDATE NEEDED` and in serial I communication I see:

``` bash
Recv: echo:MMU2:>X0*4c.
Recv: echo:MMU2:>S0*c6.
Recv: T:19.8 /0.0 B:23.0 /0.0 T0:19.8 /0.0 @:0 B@:0 P:24.8 A:28.7
Recv: echo:MMU2:Version mismatch, last bytes: 6b 6f 6b 6f 6b 6f 6b 6f 6b 6f 74 73 00 00 00 00
Recv: echo:MMU2:MMU FW UPDATE NEEDED
Recv: retryAttempts=3
Recv: echo:MMU2:<stokokokokok.
```

Do you know how I can check what is sent via MMU to my MK3S to debug it? I tried adding some code to debug, but I did not see anything in serial communication:

``` diff
--- a/Firmware/mmu2_protocol_logic.cpp
+++ b/Firmware/mmu2_protocol_logic.cpp
@@ -213,6 +213,11 @@ StepStatus ProtocolLogic::ProcessVersionResponse(uint8_t stage) {
         SendVersion(stage);
     } else {
         mmuFwVersion[stage] = rsp.paramValue;
+        MMU2_ERROR_MSGRPGM(PSTR("Version test"));
+        SERIAL_ECHOPGM("Stage: ");
+        SERIAL_ECHOLN(stage);
+        SERIAL_ECHOPGM("Number: ");
+        SERIAL_ECHOLN(mmuFwVersion[stage]);
```

I'll try to find some old thermistor and connect it to test your precompiled firmware to rule out fired chip for communication.

cjbaar, 2023-01-14:
I have not tested this with non-prusa firmware. I am guessing it want something specific from the MMU, so you would need to disable that in your printer firmware, or compile a version of the MMU firmware that gives it the version it wants, but I can't guarantee that would work.

grzlus, 2023-01-14:
But I forked your repository and only changed some values to work with thermistor.

And my changes should not affect MMU communication.

cjbaar, 2023-01-15:
What do you have in `version.h` for the MMU? I use the following:
```
static const uint16_t fw_version = 111; //!< example: 103 means version 1.0.3
static const uint16_t fw_buildnr = 505; //!< number of commits preceeding current HEAD
```
My guess is the printer wants at least 105 for `fw_version`, possibly 106.

grzlus, 2023-01-16:
I did not built MMU firmware, but I'll do that. It's a good starting point and I'll try to find the cause there.

grzlus, 2023-04-01:
So... I was using wrong branch on the other repo. Now It's fine. I had some problems with different printed parts, but overall it's a great project. I'd like to check how MMU3 looks like and adapt it to that, at least the 12 colors part :)

When I'll have time, I'll update my MK3 to MK3.5 and I'll begin testing.

Closed 2023-04-01.

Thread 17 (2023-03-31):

mmu12x-lower-mod.stl is damaged

renoxray, 2023-03-31:
Hi @cjbaar,

I finally trying to build one mu 2x based on my exist mmu2s and I found the mmu12x-lower-mod.stl come with only 78.6k size.

Could you help to update it :)

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

grzlus, 2023-04-01:
This looks like a modifier to the file `mmu12x-lower.stl`. You can use it to disable or enforce supports

renoxray, 2023-04-02:
@grzlus

Thanks for the help. I've just realized the mod part is for this purpose.

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

Closed 2023-04-02.

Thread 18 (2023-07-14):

MMU-12x stuck in "Initializing"

Agent-Cain, 2023-07-14:
I've build the MMU-12x and flashed the firmware with display on it.
Display turned on instantly.
Also flashed the 3.11. FW on the printer, no problem here.
Printer shows under "support" MMU2 N/A, not sure if this is right.

Now if i start up the printer (with the mmu) the LEDs flash from right to left, none stays on.
The display shows Initializing and none of the buttons does anything.
When I unplug the connector from the mmu to the printer nothing turns on, so I'm relatively sure that the wiring is correct.

What am I missing 🤔

Hope someone is still active here, thanks in advance !

Agent-Cain, 2023-07-15:
After some fiddeling around I found some things out:
Normal FW on Printer and MMU2 will work together, so connection is ok.
Custom cjbaar FW on Printer with stock FW on MMU establishes also a connection and works so far.
Custom cjbaar FW on printer and cjbaar FW with display on MMU doesn't work. Seems like Printer and MMU do not establish a connection.

But the cjbaar FW on Printer and the cjbaar FW without display on the MMU are working together, and the first print with it is runnung right now.

So there seems to be a problem with the display version of the FW, in my case it doesn't establish a connection and is stuck in Initializing and won't respond to any button presses. Someone else out there had the same problem and found a work around ?!
Would appreciate it if you would let me know, thanks :)

grzlus, 2023-07-31:
Yeah, I had some problems, but it was only with custom built, as I needed things for Mosquito Magnum, firmware by myself. I fixed it by using correct branch.

cjbaar, 2023-08-20:
Sorry, I don't have a good answer for you. I'm just looking through the routines it runs through in startup. After initializing, it should try to home I think, but I am not sure I see where it would get hung up there.

Agent-Cain, 2023-10-27:
Oh dang, sorry for the late response.
It doesn't even home 😅

grzlus, 2023-10-27:
Start with the [fix](https://www.printables.com/model/620818-mmu2-5-volt-power-fix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) as it might be the case of your problems with homing. On x12 hardware I had a problem with frequent restarts. More frequent than with original one. At least this will eliminate most of your problems.

I installed some DC-DC StepDown to 5V and I'm now having stable 5.2V on the line and no restarts at all.

Agent-Cain, 2023-12-29:
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

That was way over the top I wanted to do with my board :D
I got some prints out of the 12 color unit without any trouble (running the non display verison).
Today I received my PD Board from Aliexpress, which seems to be a lower hanging fruit.
After I've installed that I'll give the display version another try!

Agent-Cain, 2023-12-29:
So, even the PD-Board didn't change a thing of my problem.
Still no movement on a button press or anything., still flashing lights from right to the left but none staying on.
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
Just stuck in this stage, no operation possible.
Now that I familiarized with the MMU and their operation I noticed something more:
With the display version of the software the menu on the Prusa doesn't show certain options like "Load Filament" or "Load Filament to the Nozzle".
As I have printed already a few things on that MMU I'm sure everything is working and correctly wired.

So to me it seems like the MMU gets stuck somewhere, is there a possibility to debug it somehow ?
I really would love to get this version with the display up, every kind of help is welcome :)

Thanks in advance

flinke-flasche, 2023-12-29:
Does your MMU2 work with the firmware without display?

flinke-flasche, 2023-12-29:
I try a fix for the 5V problem as well, because my selector stucks.
I follow the guide in Chris' YouTube video.

I had an issue with the cable I soldered on my first try.
At this time my mmu2 didn't work. When i unpluged my cable and tried it again it worked again.

Maybe its a problem with the cable to your display?

Agent-Cain, 2023-12-29:
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

As the display works (kind of with the display fw) but the mmu not I would guess its not a cable related problem.

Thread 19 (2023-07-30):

mmu3

Dutchy1969, 2023-07-30:
any chance we get a fork of the mmu3 firmware and i think 3.13 for the mk3s+ and mk4 support?

i was hoping to get rid of my mk3s+ and move it over to the mk4 i started looking at the firmware and stuff but im not smart enough for that.

grzlus, 2023-07-31:
I was thinking on porting changes here to TZB firmware, but porting it MMU3 might be better idea.

I want to buy MK4 upgrade too (MK3.5 probably), but I need to find more free time for that 😀

cjbaar, 2023-07-31:
I have not yet dug into the code, but the MMU3 is a complete re-write, with a total overhaul of the communication protocol. I am guessing it won't make much sense to move my changes into it, because I did a lot of re-writing of the MMU2 code. Also, they have not yet announced what the "Mk4" version of the MMU3 will be. It is my understanding that the printer itself is not a lot more in control of that the MMU does. I am also willing to bet that they still have things like max extruders hard-coded, which could make things tricky.

Once I get the new MMU (probably September) and have a chance to play with it, I will probably decide what to do with this project, and whether or not it can be adapted to the Mk4. Most likely, given that Prusa has added interaction with the printer for troubleshooting, my screen concept will be unnecessary. This would mean the shortest path to compatibility would be minor modifications to the MMU code (rotation directions, distance between filaments, etc), but probably more significant changes to the actual printer code. Also, given that they moved away from Arduino IDE as a compiler, which I am very familiar with, there will be an additional learning curve for me.

greenfox1505, 2023-08-07:
Would it make sense to re-implement an MMUx12 from scratch? Sure, a MMU3 upgrade would be ideal, but I don't know if it's necessary. Arduinos and stepper drivers are easy to get. I've got a hand full of old RAMPS boards laying around.

grzlus, 2023-10-30:
I'll be upgrading to 3.5, so I'll need MK3 upgrade. I'll reuse as many files from current MMUx12, so the original firmware will be only patched to use correct rotations as we have them in the files. I'll probably abandon that firmware, as it will too much to patch changes made by Prusa and it's easier to start from scratch with firmware.

Dutchy1969, 2023-11-10:
I can’t wait to have a solution for the 4. I appreciate you guys help. I’m not smart enough for this stuff but if there is anything I can do to help you guys out to get this to work on a Mk4 you let me know.

grzlus, 2024-02-23:
@Dutchy1969 I'm waiting for my order to be delivered. I'm getting MK3.5 and MMU2S to  MMU3 upgrade.

In a month I should have it delivered and put together :)

grzlus, 2024-03-06:
@Dutchy1969 good news, my 3.5 and MMU3 upgrade was shipped :)

sithlord48, 2024-05-01:
TLDR: For an MK3.5+ solution or one allowing the user to use the newer MK3S firmware 3.13+
This firmware must be rebased upon the MMU's 3.x series, or otherwise implement the bi directional communication so the printer can talk to the mmu in the way it expects. Devs could upgrade their MK3S to firmware 3.13 to test an Mk4 or MK3.5 is not required.

There are Two main changes for MMU3

1. [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](https://www.prusa3d.com/en/product/mmu-pd-board-addon) A board that goes between the mmu and the printer
    - Stabilizes the power to the mmu
    - Replaces the wires that connect the mmu with a single cable. (Store: [Mk3S Wire](https://www.prusa3d.com/en/product/mmu3-printer-cable-einsy/). Currently no Mk4 link)

2. Firmware changes to both the MMU (3.x series) and the Mk3S(3.13.x)
   - Printers with firmware 3.13.0 or higher REQUIRE the MMU to use 3.x firmware
   - Enables bi directional communication so the printer can now show mmu errors on the screen. and tell the mmu to retry. No more mmu light based error codes to for those mmu issues!!
   - The MMU can be enabled and disabled from the printers menu
   - The printer can send firmware to the MMU to upgrade its firmware when you upgrade the printers (an additional .hex for the mmu firmware is included in the mk3S+ mmu package now)

The rest of the new MMU3 stuff does not matter for this project since its all printed parts. A better idler, housing lid etc.. that will not be used in this project.

For my Mk3S+ MMU2S I got the new power board and I was then able to use the 3.x firmware. Since then i have been using the " MK3S+ MMU3" profile without issue

For the MK4 / 3.5+ the only change to the MMU3 (kit) is the wire you use to hook it up to the printer.

Johnday29, 2024-07-05:
Just checking in here.  Let me say your mods to the MMU2 have been a game changers for my little 3D printing business, so Big thank you to @cjbaar .  That being said I have upgraded a couple of my printers to MK4 with MMU3 and must say it is night and day difference the speed and quality of prints I get, This means I really want to upgrade my MMU2 x 12 to MMU3 x 12.  Has there been any progress in this area?  Would be happy to contribute to make it happen. Thanks!

cjbaar, 2024-09-27:
Sorry @Johnday29. I'm glad you have used the 12x successfully. I have not had any chance to look into what it will take to get this working with MMU3.

Johnday29, 2024-09-28:
Thanks for the reply. Please let me know if I can contribute to the effort
to get this going with the mmu3 software. It runs so much smoother and with
Mk4 compatibility it is so much faster would love a boost to the 12x 😎.

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

3d-gussner, 2024-09-30:
@cjbaar The new MMU firmware has way less hard coded values and lot of that can be defined in https://github.com/prusa3d/Prusa-Firmware-MMU/blob/main/src/config/config.h and https://github.com/prusa3d/Prusa-Firmware/tree/MK3/Firmware/mmu2/variants and https://github.com/prusa3d/Prusa-Firmware/blob/MK3/Firmware/variants/MK3S.h#L673

Also have a look at https://prusa3d.github.io/Prusa-Firmware-Doc/Prusa-Firmware-MMU/index.html

But i doubt that you get the LCD display working as it consumes too many resources.

Here a build output of MMU3 _3.0.3

```
[build] AVR Memory Usage
[build] ----------------
[build] Device: atmega32u4
[build]
[build] Program:   28370 bytes (86.6% Full)
[build] (.text + .data + .bootloader)
[build]
[build] Data:       1669 bytes (65.2% Full)
[build] (.data + .bss + .noinit)
[build]
[build]
[build]
[build]    text	   data	    bss	    dec	    hex	filename
[build]   27678	    692	    977	  29347	   72a3
```

cjbaar, 2024-09-30:
@3d-gussner That does look halfway promising. I do see variables for the selector start position and distances. It looks like the idler creates a hard-coded array of positions, instead of just constant motor steps. This can be created, but might take  some tweaking. One thing I don't see is an easy way to reverse the motor directions, since some of mine are on opposite sides than the original. Maybe if you see that, let me know.

The bigger issue, then, is on the printer side itself. Will the printer accept 12 tools? The older firmware was hard-coded to throw away any g-code above T4, and also would only display sinlge-digit numbers on the screen. Any idea what that code looks like for the Mk4 board?

cjbaar, 2024-09-30:
@3d-gussner OK, according to axis.h, `dirOn` might actually reverse the motors

cjbaar, 2024-09-30:
And, of course, there is this warning. :)
```
/// Max number of extruders/tools/slots
/// Beware - if you change this, the EEPROM structure will become invalid and no migration procedures have been implemented.
/// So if you really have to change this, erase your EEPROM content then.
static constexpr const uint8_t toolCount = 5U;
```

cjbaar, 2024-09-30:
See its a quick scan of the buddy firmware showing things like this that makes me think the printer won't cooperate without a lot of changes.
```
enum class Tool {
    Tool1 = 0,
    Tool2 = 1,
    Tool3 = 2,
    Tool4 = 3,
    Tool5 = 4,
    None_Any = PrusaToolChanger::MARLIN_NO_TOOL_PICKED, // Park value
};
```
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
cjbaar, 2024-10-28:
@Biertram Nice job

Biertram, 2024-10-28:
Thank you.

I don't quite remember what the issue with V3.0.3 was, but maybe going back to V3.0.2 might fix your communication issues as well.

I just tried flashing my MMU with my V3.0.3 version, but this time it worked... Strange...
I did change the version number to go with the check in my MK3S though, so I didn't have to reflash it as well.

cjbaar, 2024-10-28:
@3d-gussner So it looks my communication issues are the result of a bad resistor on the board. The TX line (R2) should be 22ohm, but is measuring well over 1K. For whatever reason, the Mk3 works find with this, but the Mk4 drops bytes.

3d-gussner, 2024-10-29:
@Biertram Thanks for sharing.

3d-gussner, 2024-10-29:
@cjbaar I looked at my rev 0.3 board and `R2` is labeled as `022` the same as `R1` next to it. This matches also the [schematics](https://github.com/prusa3d/MM-control-2.0/blob/master/rev.03/MM-control.pdf)
With my cheap multi-meter (set to 2000 Ohm or 200 Ohm) I measure 23 - 26 Ohm on both `R2` and `R1` when disconnected from the printer. Never tried to use this board on the MK4 to see if there is a difference.

Replacing the tiny 0603 `R2` resistor isn't fun.

How do you connect the rev 0.3 board to the MK3S? Using the MMU2S cables or new PD board and matching cables which are part of the MMU2S to MMU3 upgrade?

Not sure but the PD board also has some components on the TX RX lines and these may have "tighter" tolerances what is expected.

3d-gussner, 2024-10-29:
@Biertram memory dumps are really hard to read and it doesn't make sense in this case.

>Here I kept .stepsPerUnit = (200 * 8 / 19.147274), instead of .stepsPerUnit = (200 * 8 / 37.384921), as the former worked quite well for me.

This value should be changed as the pulley diameter is different than the stock one.

Biertram, 2024-10-29:
Oh right... I confused pulley diameter and selector angle when I did the configuration...

The original value didn't give me any trouble yet. But I'll change it to 37.384921 to account for the diameter.

3d-gussner, 2024-10-29:
@Biertram The new MMU firmware is more forgiving on how much filament has been pushed/pulled. It relies more on the states of the FINDA and FSensor than the actual length pushed or pulled. You may be lucky in the previous configuration that the FINDA and FSensor triggered in the thresholds.

cjbaar, 2024-10-29:
@3d-gussner  > How do you connect the rev 0.3 board to the MK3S? Using the MMU2S cables or new PD board and matching cables which are part of the MMU2S to MMU3 upgrade?

Excellent point. I am connecting to the Mk3 with the legacy connectors, so it is probably the PD board that has issues with the faulty resistor. It's not a big deal for me, as I currently don't plan to upgrade my Mk3, but wanted to make sure it wasn't an issue for others trying to upgrade. Thanks for the input.

3d-gussner, 2024-10-30:
>How do you connect the rev 0.3 board to the MK3S? Using the MMU2S cables or new PD board and matching cables which are part of the MMU2S to MMU3 upgrade?

I used the MMU2S cables to connect the rev 0.3 board to the MK3S and it works.
As I have the new MK3S to MMU3 PD board cable I use that one as the PD board improves the Power Delivery.

I have been looking for the differences of the rev 0.3 vs 0.4.4 and I found that the F2 fuse is different
- 0.3 has a 750mA `b0075`
- 0.4.4. has a 1.5A `b150 24`

Guess that the bigger fuse improved the usage of the MMU2/S on the 12V MK2.5/S printers

>Excellent point. I am connecting to the Mk3 with the legacy connectors, so it is probably the PD board that has issues with the faulty resistor.

I measured the resistance with my multi-meter between the MMU connector TX / RX pins and MK3.5/S, MK3.9/S and MK4/S Connector TX / RX pins on the PD board and get ~330Ohm.

This means

```
MMU <-----------> MK3S no PD
TX  -> 22 Ohm  -> RX
RX  <- 22 Ohm --- TX

MMU <----------> PD board <-> MK3S with PD
TX  -> 22 Ohm -> 330
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

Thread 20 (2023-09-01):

print request

yahbluez, 2023-09-01:
Hi

I like to add this filament changer system as a kind of his own to this list of filament changers:

https://www.printables.com/model/567217-4-color-transition-module

Is it possible to print the 4 color test and give me the data to add them to the list?

I would give a backlink to this github or to the printables project if you like to have one.

cjbaar, 2024-10-18:
The data would the same as the Mk3+MMU2 or Mk4+MMU3. The new MMU3 firmware is the same as stock Prusa, with different config for the 12x spacing. But the operation is identical, so it wouldn't affect waste or print time.

zonkie, 2024-10-19:
Wow, thanks for putting all this effort Into this project! Maybe i will try it again with the mk4s and mmu3 :)

Closed 2024-10-24.

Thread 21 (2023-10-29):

PrusaSlicer custom G-code?

minu8702, 2023-10-29:
Thank you for making such device cjbaar!
I have managed to build mmu12x and flash firmware on both MK3s+ and new MMU12x.
But I am having some trouble where I am getting "File Incomplete. Continue anyway ?" error on the printer screen.
When I try with Octoprint, it says there is no tool exist, e.g. T11 for extruder 12.
I have expanded the number of extruders under 'Printer Setting'>'General'.
Also added below G-code under 'Custom G-code'>'Start G-code' for extruders 6-12, as I thought it was necessary.
M403 E5 F{"" + ((filament_type[4]=="FLEX") ? 1 : ((filament_type[5]=="PVA") ? 2 : 0))}
.
.
.
M403 E11 F{"" + ((filament_type[4]=="FLEX") ? 1 : ((filament_type[11]=="PVA") ? 2 : 0))}

If I use normal printer & MMU preset for 5 filaments, it works perfectly, but once I expand the number of extruders, I get the above error.
Do I require any other changes? or does the printer profile need to be made ground up?

Any help would be very appreciated.

minu8702, 2023-10-30:
Actually, just had to use older version of PrusaSlicer and just worked.

minu8702, 2023-10-30:
Actually, just had to use older version of PrusaSlicer and just worked.

cjbaar, 2023-10-31:
The printer firmware has a hard-coded value to search for the "end" of the g-code, which is "M84." Slicer adds a lot of comment stuff after that, and newer version of slicer keeps adding more. In my version of the printer firmware, I increased the size of the loopback from 10,000 characters to 25,000. However, it sounds like maybe this is not enough anymore. If you are compiling the printer firmware, you can try increasing the value of END_FILE_SECTION (in config.h, I think). Otherwise, try removing all the comments from the end of the generated g-code file.

`#define END_FILE_SECTION 25000 //number of bytes from end of file used for checking if file is complete`

Closed 2023-10-30.

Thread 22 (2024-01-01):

cad file for the 12 filament inlet

Dutchy1969, 2024-01-01:
I'm about to mount mine in a enclosure, instead of reinventing the wheel can I get the cad file for the 12 filament inlet so I can modify it for the prusa original enclosure?

Dutchy1969, 2024-06-10:
can be closed, sold the enclosure, so have no way to test it even if I had it

Closed 2024-10-18.

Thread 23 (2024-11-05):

Umbau mmu3

Lanzelott76, 2024-11-05:
Hallo
Wird die Hartware von der mmu3 dort nur genommen oder geht die von der mmu2s auch dafür .
Wäre es möglich eine Klipper Lösung zu finden für den Umbau auf 12 Farben ...das wäre super .
Gruß

cjbaar, 2024-11-05:
I believe the firmware I have posted for the MMU3 should work with the previous hardware, but I have not tested it. There have been no changes in the size or distances between filaments. Also, I am not familiar with Klipper, but generally the printer firmware just needs to forward all T commands to the MMU without restriction.

Lanzelott76, 2024-11-05:
Wenn das so ist werde ich mal die neuen Teile drucken und den Umbau wagen .
Danke für die schnelle Antwort. 😉

3d-gussner, 2024-11-06:
The internal communication between the printer and MMU changed.
In the 1.0.6 version the printer send
`S0` to get the Major version number

The new version 3.0.x has an additional CRC checksum
`S0*c6` to get the Major version number

@Lanzelott76 If you find any Klipper solution that works with the MM-control board please let us know. Viel Glück bei der Suche.

Lanzelott76, 2024-11-06:
Nein , die original Platine geht nicht auf Klipper zu flashen...es gibt nur eine Lösung mit einem anderen Bord (skr mini e3 v2) wo man die Klipper Firmware drauf bekommt und die mmu mit steuert .
Ich werde mal schauen ob man die jetzige Klipper Version umschreiben kann von 5 auf 12 Stationen .
Gruß

3d-gussner, 2024-11-06:
@Lanzelott76 I continue writing in English if that is okay.
I have not worked on Klipper but if you can establish a second serial communication to the MM-conrtol board from Klipper and "replicate" the protocol it should be doable to get Klipper "talking" to stock MM-control board.
I can imagine that it is hard to get Klipper firmware on the 32u4 chip which is used on the MM-control board. It doesn't have that many resources.

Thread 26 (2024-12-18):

MK3.5S with MMU3 x12

VSCustoms, 2024-12-18:
Just curious if any got the MMU3 x12 working on a MK3.5S firmware?
 I just picked up a MK4S I’m going to get running the MMU12 on but would also like to upgrade my MK3S to the MK3.5S and the MMU3 x12 setup as that is one area I find an issue is the MMU needs just a little more power.

Any help would be amazing.

cjbaar, 2024-12-19:
I personally have not. I have only run the MMU2-based firmware with a Mk3 (up to 3.11 I think), and the MMU3x12 with a Mk4. However, there is no difference in the MMU firmware for different printers, so the MMU side should be fine. The only thing is the Mk3 firmware still cuts off anything in g-code above T4. You can see if this works: https://github.com/3d-gussner/Prusa-Firmware/releases/tag/c3.14.1_MMU12x

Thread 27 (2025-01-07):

12x12x5 drive gear

HonzaJaros, 2025-01-07:
Hi,

just noticed the eBay link was removed due to the price, there was like $500 on that.

I spoke with seller of this:

https://www.ebay.com.au/itm/355753143663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

It’s out of stock, but if you text them, they open the QTY just you need and backorder it for you. 1-3 weeks they said.

12x costed 53 bucks

ino89, 2025-01-07:
Hello together in Germany you can buy the one here

https://www.roboter-bausatz.de/p/mk7-mk8-extruder-vorschubrad-fuer-1.75-3mm-filament-40-zaehne-5mm-bohrung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

momorox, 2025-01-08:
@ino89 Unfortunately, it looks like the height is 11mm, not 12mm.

HonzaJaros, 2025-01-08:
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

I asked especially

jasonmatthews41, 2025-01-08:
In my opinion, the 11 mm ones work just fine. I have had zero issues, and I have done dozens of prints already.

HonzaJaros, 2025-01-08:
I have ordered them and the rest if needed hardware too so there is no way back and I’ll make it work.

I just wanted other ppl know they provide them even they are not in stock…

just off topic, is there a discord or fb page to discuss about this?

momorox, 2025-01-09:
Nope. Also, I was actually referring to the link that ino89 posted.

MagnusVesper, 2025-05-23:
Would this work? They look more like the ones used on the stock MMU3. But they're 13mm wide.
https://www.amazon.com/uxcell-Drive-Direct-Extruder-Reprap/dp/B07Y9Z77LV

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

jasonmatthews41, 2025-05-23:
Those will not work. The entire piece needs to be splined. Some of them will grab more than one filament at a time.

MagnusVesper, 2025-05-23:
Ah, thanks. Does that mean I could use fully splined drive gears of any width as long as they add up to 84mm?

cjbaar, 2025-05-23:
The reason I went with the other style (I forgot what printer brand uses them now) is that each gear works on two filaments. The 6mm spacing was based on the gears being 12mm wide. You just need to make sure a grub screw isn't lined up with one of the filaments.

MagnusVesper, 2025-05-24:
I asked in a maker group I'm in and got some useful info:
A gear with teeth like that is a "spur gear" and the term for having teeth along the whole width is "hubless"
But these aren't actually gears, because the teeth are pointed. They are "feed wheels" or "feel rollers".
This specific kind with a grub screw and straight teeth seems to be mainly used for 3D printing, so just "extruder wheel" may be the best term for them.
Hopefully these names will make it easier to find the correct kind.

AnatomicFlack, 2025-07-04:
Would this work?  The only issue I could see is they are 11mm diameter (which seems to be most of the available offerings anywhere), but the fact that it's wire cut and that the teeth go all the way to the end of the unit seems like it would be beneficial.

https://www.aliexpress.com/i/2251832348720735.html

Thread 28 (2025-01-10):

MK4 BSOD - Multiple CFSR Errors

momorox, 2025-01-10:
Whenever I try to print something, a few minutes in it crashes. This even happens when I try to print with only one color. I tried the firmware posted here as well as one I built myself. If I disable the MMU and bypass it, the printer functions normally.
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

Printer: MK4S
Firmware: 6.1.4
Buddy Board: 37

MMU3
Firmware Version: 3.0.3
MMU Board Revision: 0.4.4

jasonmatthews41, 2025-01-10:
I might be wrong here, but are you running a MK4 flash on your MK4S? It could be that. I am running a full MK4S flash on my MK4S. I've never had a single problem.

momorox, 2025-01-10:
I don't think that's it. The MK4 and MK4S use the same firmware. You set it to the MK4S through the settings.

jasonmatthews41, 2025-01-10:
It's not exactly the same firmware. I found out the hard way, that the MK4S absolutely must have the silicone sock, or you burn up thermistors, and heaters. I went through two thermistors and a heater cartridge before I figured it out. Also, make sure that with the MMU setup, you have to use the regular brass nozzle, and not the high flow one. The tiniest little things make all the difference in the world with this setup.

momorox, 2025-01-11:
None of these are the issue.

momorox, 2025-01-12:
What revision is your Xbuddy Board? You should be able to see it from the MK4S under "Info"

momorox, 2025-01-12:
Is anyone's xBuddy board revision 3.7?

cjbaar, 2025-01-12:
I'm still running 6.1.3 on my Mk4. Can you try that? Or is 6.1.4 a requirement for the "S" model? The MMU firmware used for the 12x is not altered in any way, it only provides different length parameters via the config.h file. Can you ask Prusa what that stack trace means?

momorox, 2025-01-12:
MK4S doesn't require 6.1.4 and I tried 6.1.3. I'll ask, although I think it stands for Configurable Fault Status Register.

momorox, 2025-01-15:
It turns out my xBuddy board was defective. I replaced it and it now works.

Korri, 2025-01-17:
I had the same issue on my MK4S, and upgrading to the `rc1` fixed it for me too, thanks for updating!

Closed 2025-01-15.

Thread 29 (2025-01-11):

Clone by aliexpress

ino89, 2025-01-11:
Hello everyone,

Can you buy a clone and use the parts?
and take a used mmu2 apart

I could get a used mmu2 and then would the clone parts. Buy for this

https://a.aliexpress.com/_EulmqHO

cjbaar, 2025-01-12:
The key is whether the power board is up to spec. The physical parts should be fine.

Closed 2025-01-28.

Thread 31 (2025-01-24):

T40 Drive Gears not pushing filament to the Selector

edirian000, 2025-01-24:
Hello, I've tried everything i can think of to resolving this issue but have been unable to. Hoping someone out there can assist me. When trying to start a print the gears aren't catching the filament and pushing it to the selector... Not sure why when taking a closer look everything looks fine but looks like the gears are just rubbing against the filament and not acutally pushing it forward.. Does anyone have a solution to resolving this by any chance?

ino89, 2025-01-24:
Did you pull the screws a little tighter?

edirian000, 2025-01-25:
I did, seems to be pulling a bit more, but now the finda sensor keeps saying it cant trigger... not sure why it wont see the filament passing it.

jasonmatthews41, 2025-01-25:
Probably a stupid question, but did you lower the sensor far enough for it to read the ball bearing?

edirian000, 2025-01-25:
ball bearing?? i dont believe my mmu3 came with one lol, was it suppose to?

jasonmatthews41, 2025-01-25:
Yes. It comes with a ball bearing that triggers the sensor with magnetism. I'm including a couple of photos. Just underneath the sensor there should be the ball bearing to trigger the sensor.

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

edirian000, 2025-01-25:
wow.. i had no idea, ill try to find it and let ya know the results, thank you for the assistance friends ^_^

edirian000, 2025-01-25:
So the finda sensor is good now! But its back to the gears again, theyre just not wanting to pull the filament.

jasonmatthews41, 2025-01-25:
I would say try tightening the two spring screws holding down the top. Mine works just great with just a couple of threads. If it doesn't grip enough, I would tighten them a half a turn to a full turn. If the selector cannot home, then I would loosen them about a half a turn. It's a love-hate relationship with having the tensions just right. It's the only annoying part of the whole thing. I find that I have to constantly adjust mine. I was thinking about getting nyloc nuts instead of the regular plate nuts.

edirian000, 2025-02-07:
i have tried tightening the screw, but i think i might be possibly missing something? Here's some pictures of where i think something might be missing. If so what is missing though??

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

jasonmatthews41, 2025-02-07:
Yeah dude. You are definitely missing something all right. You need a ball bearing there.

Closed 2025-02-07.

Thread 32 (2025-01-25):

Crashing on filament 6

VSCustoms, 2025-01-25:
Prusa MK4S. Firmware 6.1.4. It will load filament 6 and then crash. Has happened twice so far.

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

VSCustoms, 2025-01-26:
Fixed on 4S using 6.2.0-RC1.

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

jasonmatthews41, 2025-01-26:
Hell yeah dude! You are the one on YouTube that inspired me into this entire thing in the first place.

VSCustoms, 2025-01-27:
> Hell yeah dude! You are the one on YouTube that inspired me into this entire thing in the first place.

Thanks man. Good to know. Honestly it takes a Prusa to the next level. And when just testing this MK4s has my mind blown. The new design changes on the MMU12 just work with the MMU3 and MK4S upgrades.

Closed 2025-01-26.

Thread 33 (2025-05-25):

Compatibility of MMU3-12x with custom MK3S firmware

hiroloquy, 2025-05-25:
Has anyone successfully gotten the MMU3-12x to work with custom MK3S firmware?

I'm currently using a Prusa i3 MK3S+ with an MMU2S-12x, and I’m interested in upgrading to an MK3S+ with MMU3-12x.
To that end, I’ve installed the following firmware:

- Printer: [MK3S_MK3S+_MMU12x_FW_3.14.1_MULTILANG.hex](https://github.com/3d-gussner/Prusa-Firmware/releases/download/c3.14.1_MMU12x/MK3S_MK3S+_MMU12x_FW_3.14.1_MULTILANG.hex) (by @3d-gussner)
- MMU: [cjb_fw_MMU2board_12x-nodisplay.hex](https://github.com/cjbaar/prusa-mmu-12x/blob/master/firmware/cjb_fw_MMU2board_12x-nodisplay.hex) and [cjb_fw_mmu3_3.0.3-x12.hex](https://github.com/cjbaar/prusa-mmu-12x/blob/master/firmware/cjb_fw_mmu3_3.0.3-x12.hex) (by @cjbaar)

However, the MK3S+ does not recognize the MMU (`LCD menu > Support > MMU: N/A`).
If anyone has experience with this setup or can offer any tips, I’d greatly appreciate it.

Thanks!

Simon-CR, 2025-05-29:
> [@Simon-CR](https://github.com/Simon-CR) Did you upgrade the firmware on a board that was previously flashed as MMU2? That’s where I have had the issue. And it sounds like [@hiroloquy](https://github.com/hiroloquy) maybe running into the same thing.

sadly no, mine started as mmu3.  there must be some differences between mmu2 and mmu3, @hiroloquy, does the prusa mmu3 firmware allow the mmu module to be detected properly ?

3d-gussner, 2025-05-31:
@Simon-CR Please try to connect your MK3S via USB and open a serial monitor like Putty and see what happens when you enable the MMU in LCD Settings->MMU [ON|OFF]

You should see some output like this:
```
echo:MMU2:<S0 A3*22.
echo:MMU2:>S1*ad.
echo:MMU2:<S1 A0*34.
echo:MMU2:>S2*10.
echo:MMU2:<S2 A3*70.
echo:MMU2:>S3*7b.
echo:MMU2:<S3 A380*d9.
```

`echo:MMU2:<S0 A3*22.` Is the response from the MMU that it's major version number is 3. `A`nswer = 3 plus CRC check
`echo:MMU2:<S1 A0*34.` Minor = 0
`echo:MMU2:<S2 A3*70.` Revision = 3
`echo:MMU2:<S3 A380*d9.` Build number = 380

Also always install the firmware with PrusaSlicer especially the printer firmware.

Which board version do you have?

You can also try to send `M709 X42` to erase the eeprom of the MMU, see [here](https://reprap.org/wiki/G-code#M709:_MMU_power_.26_reset)

hiroloquy, 2025-06-01:
Thank you all for sharing such helpful tips!

I had mistakenly assumed that the MK3S+ would automatically detect the MMU2S/3. However, after setting `MMU: On` via the LCD menu, the printer successfully recognized the MMU. I was then able to use both `Preload to MMU` and `Load to nozzle` functions with all 12 filaments.
At the time, I was using [`MK3S_MK3S+_MMU12x_FW_3.14.1_MULTILANG.hex`](https://github.com/3d-gussner/Prusa-Firmware/releases/download/c3.14.1_MMU12x/MK3S_MK3S+_MMU12x_FW_3.14.1_MULTILANG.hex) and  [`cjb_fw_mmu3_3.0.3-x12.hex`](https://github.com/cjbaar/prusa-mmu-12x/blob/master/firmware/cjb_fw_mmu3_3.0.3-x12.hex).

I also confirmed that the printer is properly recognized by PrusaConnect using a Raspberry Pi 4B.
Next, I’m planning to upgrade the MMU-12x body from [v1.4](https://github.com/cjbaar/prusa-mmu-12x/tree/master/stl/v1.4) to [v3.3](https://github.com/cjbaar/prusa-mmu-12x/tree/master/stl/v3.3), and test if full 12-color prints work as expected.

Thanks again, everyone!

cjbaar, 2025-06-05:
@hiroloquy Glad you got it working. I think the switch to turn on/off the MMU from the menus was added in printer 3.14 on.

hiroloquy, 2025-06-08:
@cjbaar
Oh nice, thanks for the heads-up! I didn’t know about the MMU on/off switch, so I’m glad I found out here.

Over the past few days, I’ve done a few prints with the MK3S+ and MMU3-12x, and your MMU3 firmware works really well with 3d-gussner’s custom MK3S+ firmware. It handled 3–4 color prints without a hitch—and even full 12-color prints worked perfectly!

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

Also, even with the custom firmware, I was still able to use Prusa Connect and wirelessly send files from PrusaSlicer, which is super convenient.

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

Really happy to have a more capable 12-color MMU setup now. Big thanks to you and @3d-gussner!

By the way, I didn’t use a PD board when upgrading from MMU2S to MMU3. For details, please refer to Chris’s video: [Do You Need An Upgrade? - MMU2 to MMU3 - Chris's Basement - 2023 - YouTube](https://youtu.be/JAWqIH_U66s?t=1136&si=din2Zuzi-mcL1v2n)

minu8702, 2025-09-08:
Thank you @cjbaar, @3d-gussner and @hiroloquy all for mentioning the compatibility of the new version with the MK3S+
I would not have known there was a MMU3X12 compatible firmware available for MK3S+. Have been using MMU2X12 for more than a year always wanted to update the firmware for some of the new features. Now my printer is up-to-date and MMU has been updated to MMU3.
Cannot thank enough for the convenience 12 fialment MMU is providing!!

With the compiling of the custom firmware, is there a way to compile with the thermal model for REVO hotends? I am newbie in this category and just went ahead and changed the hotend. It seemed to work at first but obviously caused thermal anomarly and eventually a thermal error. Currently running with the thermal model protection off but want to see if the firmware can be compiled with the correct thermal model.

3d-gussner, 2025-09-08:
@minu8702 Checkout https://github.com/3d-gussner/Prusa-Firmware/releases/download/c3.14.1_MMU12x/MK3S_MK3S+-E3DREVO_MMU12x_FW_3.14.1_MULTILANG.hex or https://github.com/3d-gussner/Prusa-Firmware/releases/download/c3.14.1_MMU12x/MK3S_MK3S+-E3DREVO_HF_60W_MMU12x_FW_3.14.1_MULTILANG.hex

I don't have the REVO nor the MMU12x so can't promise everything is working fine.

3d-gussner, 2025-09-08:
@minu8702
>With the compiling of the custom firmware, is there a way to compile with the thermal model for REVO hotends?

Ideally you create a copy of the https://github.com/3d-gussner/Prusa-Firmware/blob/c3.14.1_MMU12x/Firmware/variants/MK3S-E3DREVO.h with a new name `MK3S-E3DREVO_MMU12x.h` and change in the new file `#define MMU_FILAMENT_COUNT 5` to `#define MMU_FILAMENT_COUNT 12`

Then you can use cmake to cleanup the cache and then build it.

Closed 2025-09-22.

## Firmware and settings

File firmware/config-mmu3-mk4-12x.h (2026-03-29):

/// @file config.h
#pragma once
#include <stdint.h>
#include "axis.h"

/// Define Debug mode to add additional serial output

//#define DEBUG_FINDA
/// Enable DEBUG_LOGIC to compile debugging and error messages (beware of code base size ;) ) for the logic layer
//#define DEBUG_LOGIC

/// Enable DEBUG_MODULES to compile debugging and error messages (beware of code base size ;) ) for the modules layer
//#define DEBUG_MODULES

/// Enable DEBUG_HAL to compile debugging and error messages (beware of code base size ;) ) for the HAL layer
//#define DEBUG_HAL

/// Wrangler for assorted compile-time configuration and constants.
namespace config {

/// Max number of extruders/tools/slots
/// Beware - if you change this, the EEPROM structure will become invalid and no migration procedures have been implemented.
/// So if you really have to change this, erase your EEPROM content then.
static constexpr const uint8_t toolCount = 12U;
static_assert(toolCount < 15, "Up to 14 valid slots (+1 parking) is supported in EEPROM storage");

// Printer's filament sensor setup
static constexpr const uint16_t fsensorDebounceMs = 2;

// LEDS
/// The complete period of LED's blinking (i.e. ON and OFF together)
/// Beware - in order to keep the blink periods "handle" millis overflow seamlessly
/// keep the period a power of 2 (i.e. 256, 512, 1024).
/// If you don't, one of the LED unit tests will fail.
static constexpr uint16_t ledBlinkPeriodMs = 1024U;
static_assert(ledBlinkPeriodMs == 256 || ledBlinkPeriodMs == 512 || ledBlinkPeriodMs == 1024 || ledBlinkPeriodMs == 2048, "LED blink period should be a power of 2");

// FINDA setup
static constexpr const uint16_t findaDebounceMs = 100;

// Buttons setup
static constexpr const uint8_t buttonCount = 3; ///< number of buttons currently supported
static constexpr const uint16_t buttonsDebounceMs = 20; ///< tuned with a pack of highly trained monkeys :)
static constexpr const uint16_t buttonADCLimits[buttonCount][2] = { { 0, 50 }, { 80, 100 }, { 160, 180 } };
static constexpr const uint16_t buttonADCMaxValue = 1023; ///< used in unit tests
static constexpr const uint8_t buttonsADCIndex = 5; ///< ADC index of buttons input

// VCC measurement setup
static constexpr const uint8_t VCCADCIndex = 30; ///< ADC index of scaled VCC input
static constexpr const uint16_t VCCADCThreshold = 274; ///< ADC value for triggering the UV_VCC error
/// We are measuring the bandgap voltage, Vb=1.1V.
/// To compute the threshold value: `VAL = 1125.3 / AVCC`
/// So for AVCC=4.1V, you get VAL=274.46
static constexpr const uint8_t VCCADCReadCnt = 10; ///< Number of ADC reads to perform, only the last one being used

// Motion and planning

/// Do not plan moves equal or shorter than the requested steps
static constexpr uint8_t dropSegments = 0;

/// Max step frequency 40KHz
static constexpr uint16_t maxStepFrequency = 40000;

/// Minimum stepping rate 120Hz
static constexpr uint16_t minStepRate = 120;

/// Size for the motion planner block buffer size
static constexpr uint8_t blockBufferSize = 4;

/// Step timer frequency divider (F = F_CPU / divider)
static constexpr uint8_t stepTimerFrequencyDivider = 8;

/// Smallest stepping ISR scheduling slice (T = 1 / (F_CPU / divider) * quantum)
/// 25us is the max frequency interval per maxStepFrequency attainable for a single axis
/// while accelerating: with 3 axes this yields a required minimum of 75us
static constexpr uint16_t stepTimerQuantum = 256; // 256 = 128us

/// Max retries of FeedToBondtech used in LoadFilament
static constexpr uint8_t feedToBondtechMaxRetries = 2;

/// Distances
static constexpr U_mm pulleyToCuttingEdge = 5.0_mm; /// 33.0_mm /// Pulley to cutting edge.
/// Case 1: FINDA working: This should be the max retraction after FINDA un-triggers.
/// Case 2: FINDA not working: calculate retraction from printer to this point.
static constexpr U_mm filamentMinLoadedToMMU = 10.0_mm; /// Limit of retraction.
static constexpr U_mm ejectFromCuttingEdge = 40.0_mm; /// Eject should ignore FilamentMinLoadedToMMU and retract
static constexpr U_mm cuttingEdgeRetract = 5.0_mm; /// Cutting retraction distance (filament should be flush with outlet)
static constexpr U_mm cuttingEdgeToFinda = 18.5_mm; /// Cutting edge to FINDA MMU side -1mm tolerance should be ~18.5. FINDA shouldn't trigger here.
static constexpr U_mm findaTriggerDistance = 4.5_mm; /// FINDA trigger distance +1.0_mm tolerance.
static constexpr U_mm cuttingEdgeToFindaMidpoint = 3.5_mm; /// Cutting edge to Midpoint of FINDA should be 22.85_mm.
static constexpr U_mm findaToCoupler = 25.0_mm; /// FINDA Coupler side to coupler screw.
static constexpr U_mm couplerToBowden = 3.5_mm; /// FINDA Coupler screw to bowden mmu side (in coupling).
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

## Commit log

2020-04-11 adding v1.4 assets
    [mmu12x-bracket-frame.stl, mmu12x-bracket-table.stl, mmu12x-finda-wire-clip.stl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]
2020-04-13 updating selector to 2-piece design
    [mmu12x-selector-2pc-m10.stl, mmu12x-selector-2pc-m6.stl, mmu12x-selector-m10.stl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]
2021-02-18 add m5 heat-set selector
    [HeatSet-mmu12x-selector-v1.1.stl]
2021-04-15 rename firmware; add printer main
2021-04-15 add idler engaged photo
2022-02-13 add lack enclosure mods
    [cable-passthrough.stl, mmu-ptfe-pass-insert.stl, mmu-ptfe-pass-lock.stl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]
2024-10-15 prepping mmu3 artifacts
    [mmu12x-bracket-frame.stl, mmu12x-bracket-table.stl, mmu12x-finda-wire-clip.stl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]
2024-10-15 rename assembly files to readme
2024-10-18 re-org stl dir, add power cover info
    [mmu12x-bracket-frame.stl, mmu12x-bracket-table.stl, mmu12x-finda-wire-clip.stl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]
2024-10-18 add 3.3 stl files
    [mmu12x-bracket-frame.stl, mmu12x-bracket-table.stl, mmu12x-finda-wire-clip.stl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]
2024-12-17 Add a link to drive gears with the correct dimensions (#25)
    * Update README.md
    Add link to drive gears with the correct dimensions
    * Update README.md
    Add link to drive gears with the correct dimensions.
2025-12-17 add finda clamp stl
    [mmu12x-finda-clamp.stl]
